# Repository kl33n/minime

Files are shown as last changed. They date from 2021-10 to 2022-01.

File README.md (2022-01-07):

# minime



3D printer mainboard Minime + Minime_mini, using a Raspberry Pi Pico (RP2040). Can be used on top of a Raspberry Pi or as standalone USB version.

The main goal of creating this little board was to design a 3D printer mainboard with Raspberry Pi Pico (RP2040) as MCU running Klipper firmware. Because of the limited number of I/O pins and ADC pins the board results in a very minimalistic (only 4 Stepper Driver on minime_mini) but also universal PCB.

Main Features:
- Running Klipper Firmware on Raspberry Pi Pico
- Raspberry Pi Host Version = use the minime and minime_mini as 3D Printer Mainboard with all primary features, like Heat_Bed and Hotend Control, Hotend Fan and Part Fan Control, X/Y/Z Endstop reading, Hotend Temperature and Bed Temperature reading, Probe reading, controlling 4 TMC2209 Stepper Driver
- The minime board can separately be used as standalone sensor board without the need of minime_mini as driver board and can directly be connected via usb to any Raspberry Pi Host
- Switchable between Endswitch and sensorless Homing via Solderjumper
- Switchable between +5V and +24V Probe via Solderjumper
- Switchable between +5V and +24V Fan Supply via Solderjumper
- Hotend Fan (Fan1, Sunon MF40100V1-1000C-G99) uses a 3 pin Header: VCC, GND and tachometer signal for savety reasons
- Fan tachometer signal can be set up in Klipper. If the speed of the Hotend Fan is not detectable, Klipper shuts down the printer (future option)
- Integrated bat85 diode (or similar) if using +24V probe
- Raspberry Pi Pico is used with pin headers to completely exchange the module if broken

Raspberry Pi Pico (with RP2040 Microcontroller):

- Raspberry Pi Host Version --> Raspberry Pi Pico has to be flashed with klipper.uf2 (UART Communication Option)
- Raspberry Pi Pico standalone Version --> Raspberry Pi Pico has to be flashed with klipper.uf2 (USB Communication Option)

136657995-72b43971-b637-41dd-9ba2-68b54d284a6b

A special thanks goes to Matt Shepcar (https://easyeda.com/matt_1626/) for his inspiring projects "Piglet print head control board" and "Raspberry Pi G-Code HAT"!

Future Modification:
- Switch from Raspberry Pi Pico Module to RP2040 integrated circuit
- Design two RP2040 MCU board, a host version with more than 4 stepper driver as driverboard and a separat sensorboard version including endswitches/hotend/bed/fans/temperatursensors and much more

Has to be continued!

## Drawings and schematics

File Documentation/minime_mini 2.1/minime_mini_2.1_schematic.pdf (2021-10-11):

# 4 J2

# D_EN C_DIAG B_DIAG A_DIAG A_STEP

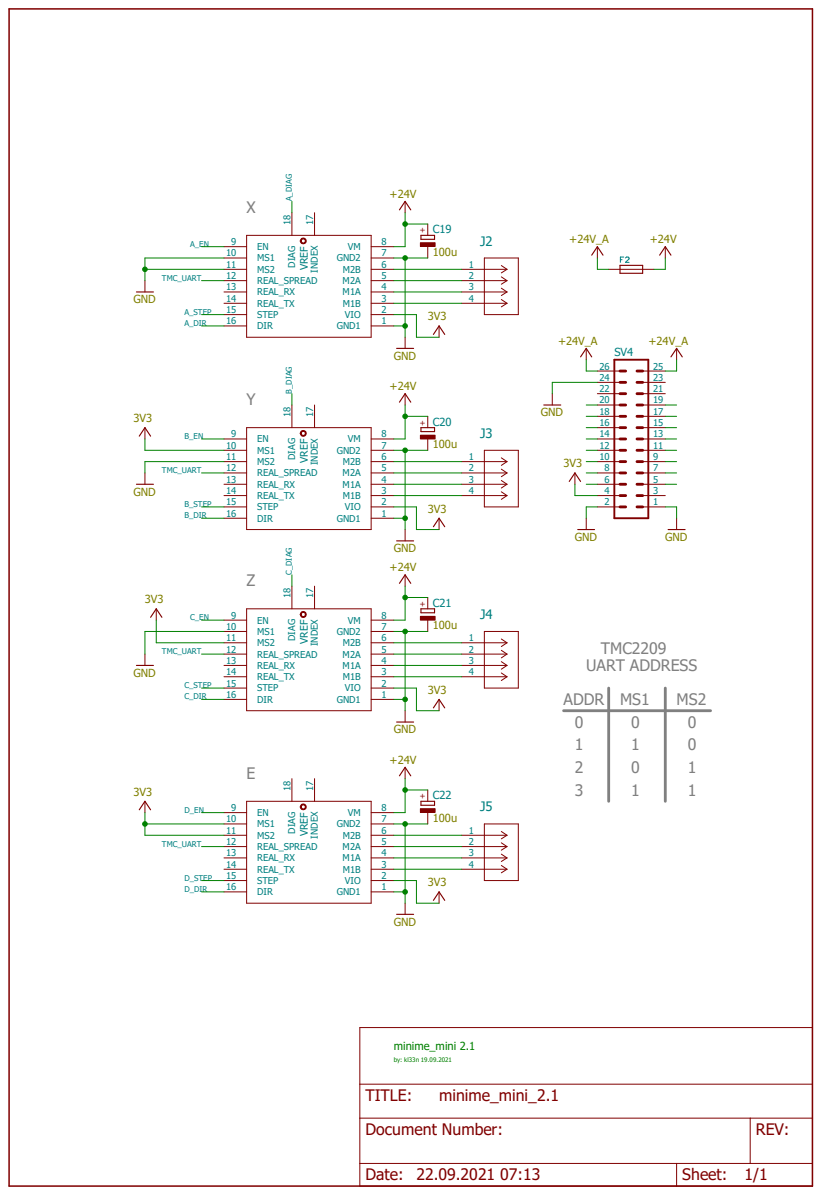
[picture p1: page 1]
GND; GND1; VIO; GND2; MS1 10 MS2 11 REAL_SPREAD 12 REAL_RX 13 REAL_TX 14 STEP 15; DIR 16; DIAG ¹⁸ VREF INDEX 17; C_DIR; C_STEP; D_DIR; D_STEP; A_DIR; B_STEP B_DIR; TMC_UART; TITLE:; minime_mini_2.1; by: kl33n 19.09.2021 minime_mini 2.1; ADDR; TMC2209 UART ADDRESS

Document Number: | REV:

Date: 22.09.2021 07:13 | Sheet: 1/1

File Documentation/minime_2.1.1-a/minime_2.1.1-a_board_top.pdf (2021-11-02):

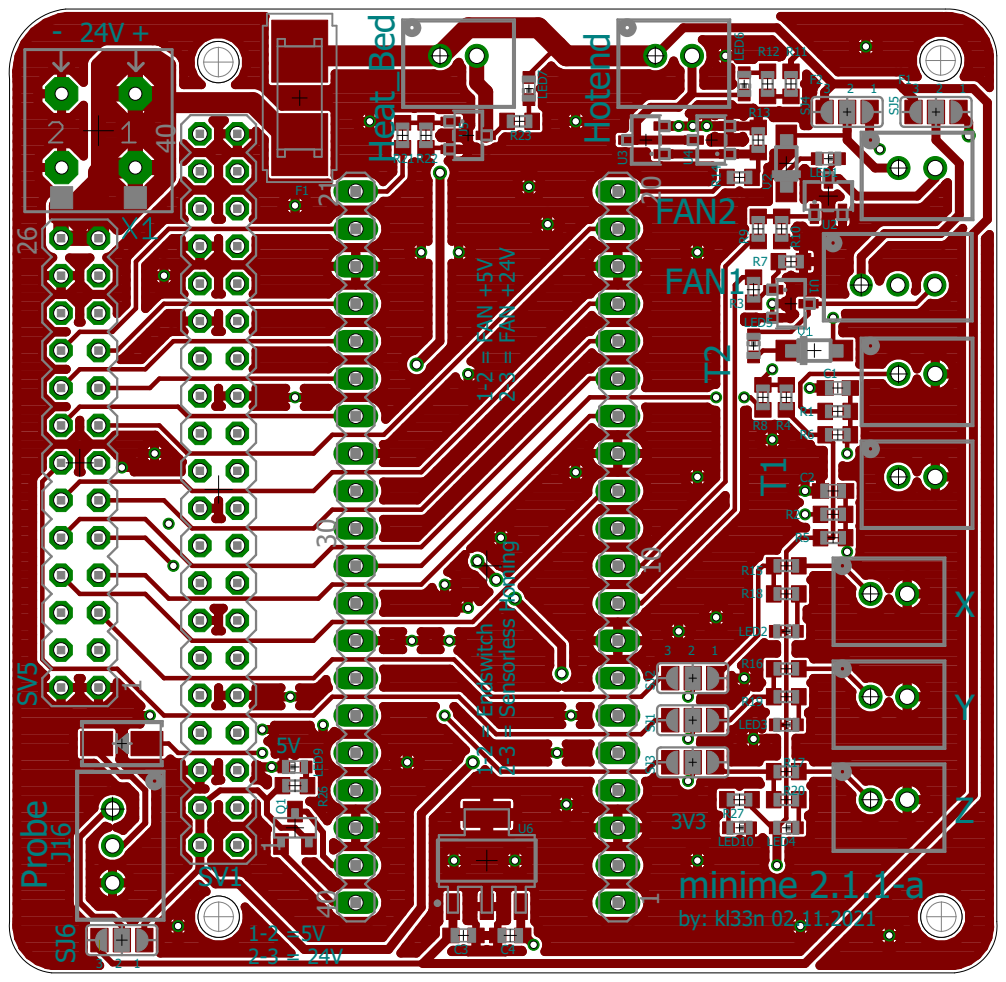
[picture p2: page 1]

1 20 10 21 40 30 1 40 1 26 - 24V + XYZ FAN1T2 T1 FAN2 Heat_Bed Hotend Probe3V3 5V 1-2 = Endswitch 2-3 = Sensorless Homing 3 2 1 minime 2.1.1-a by: kl33n 02.11.2021 1-2 = FAN +5V 2-3 = FAN +24V 3 2 1 3 2 1 1-2 =5V 3 2 1 2-3 = 24V F2 F1 R15 R16 R17 LED2 LED3LED4 R18 R19 R20 SV1 R1 R2 R3 R5R6 R7 U1 LED5 C1 C2 LED6 R12 R11 U3U4 R13 R14R21R22 U5 R23 LED7 LED9 R26 R27 LED10 SJ1 SJ2 SJ3 Q1 J16U6 C3 C4 F1 SV5 R8 R4 SJ5 SJ4 SJ6 LED1 R9 R10U2

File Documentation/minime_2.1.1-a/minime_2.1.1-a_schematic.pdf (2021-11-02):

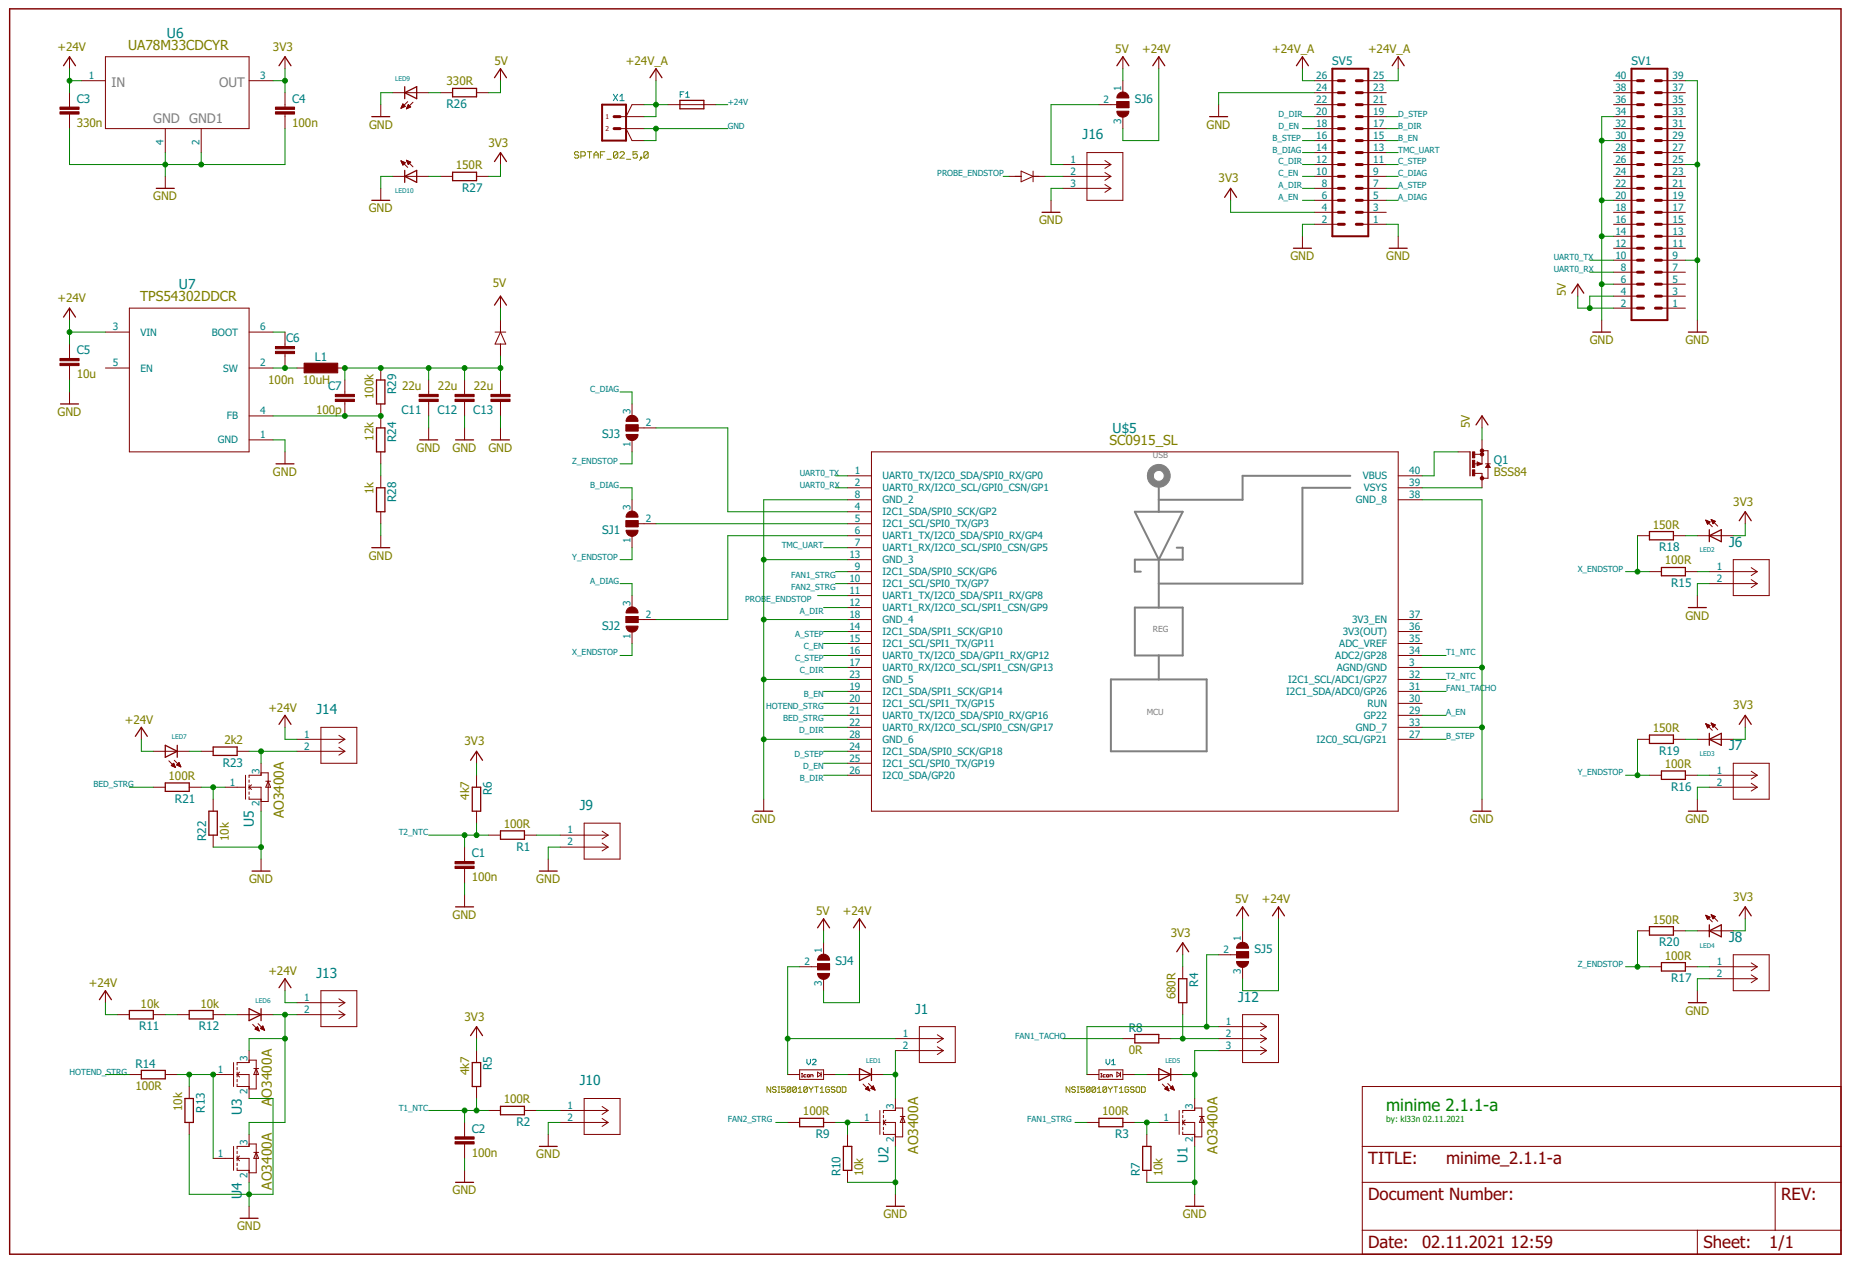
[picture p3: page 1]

REV: TITLE: Document Number: minime_2.1.1-a

Date: 02.11.2021 12:59 | Sheet: 1/1

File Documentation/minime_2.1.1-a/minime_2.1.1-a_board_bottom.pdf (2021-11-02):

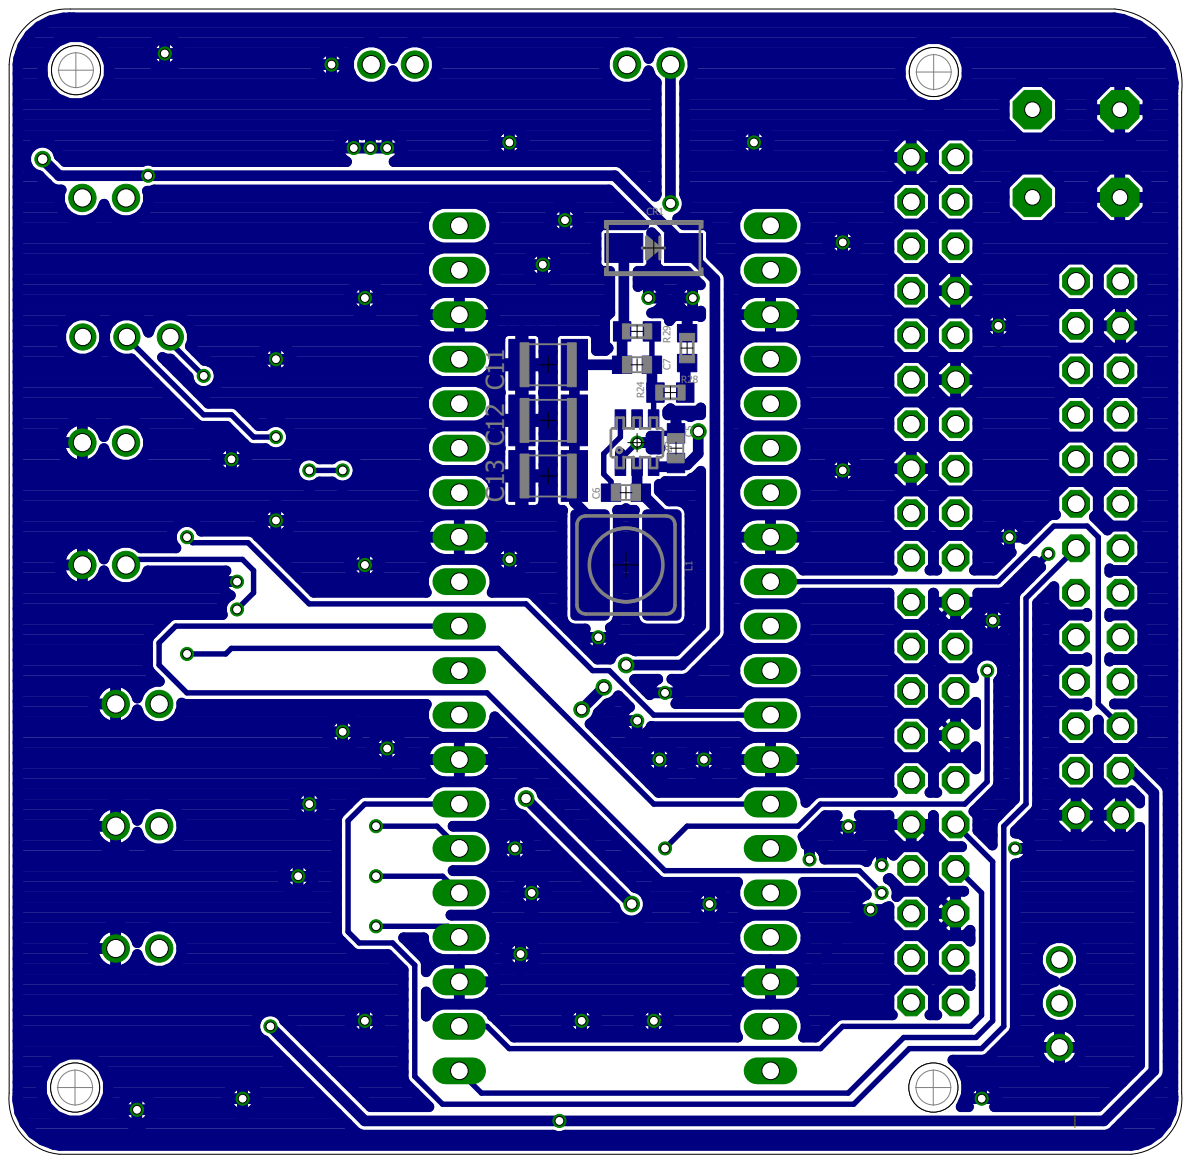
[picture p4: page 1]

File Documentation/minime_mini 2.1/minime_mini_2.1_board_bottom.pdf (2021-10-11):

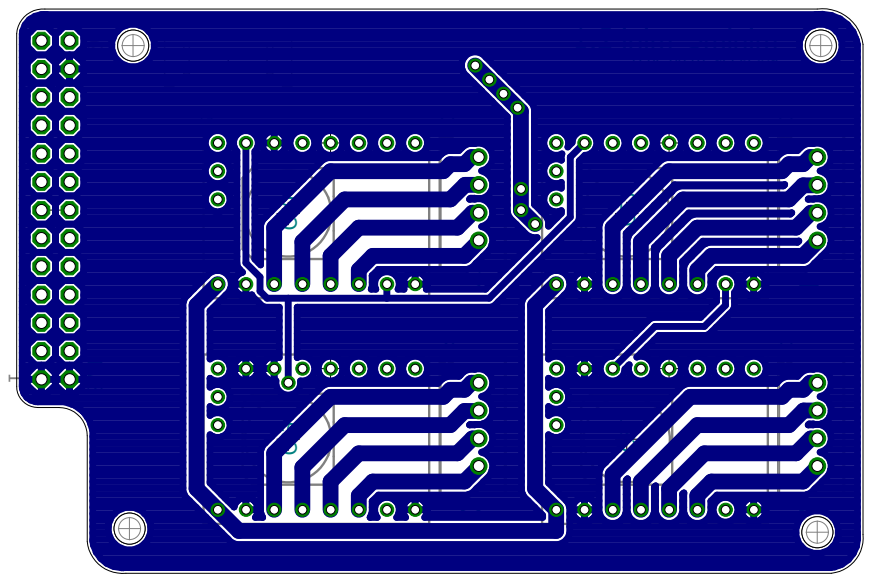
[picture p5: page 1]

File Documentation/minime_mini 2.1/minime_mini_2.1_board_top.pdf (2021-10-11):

# minime_mini 2.1

# by: kl33n 19.09.2021

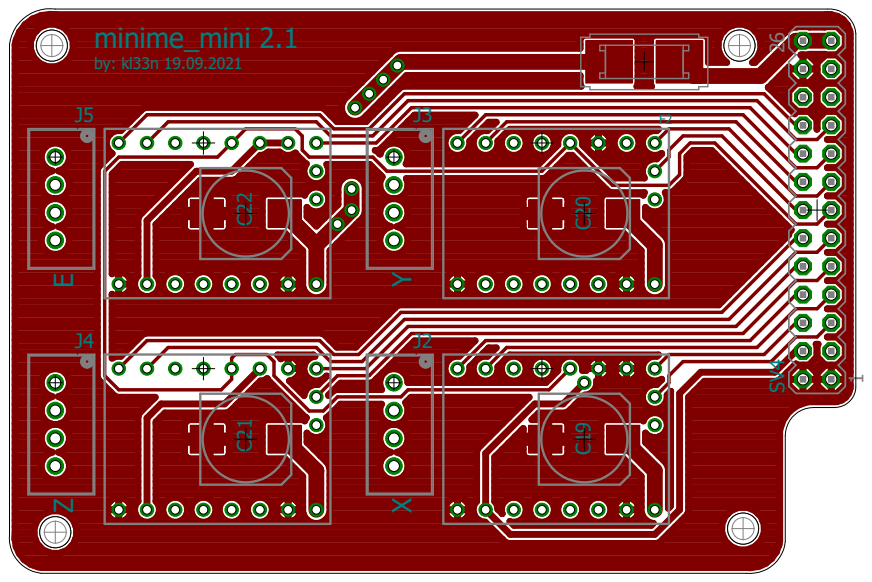
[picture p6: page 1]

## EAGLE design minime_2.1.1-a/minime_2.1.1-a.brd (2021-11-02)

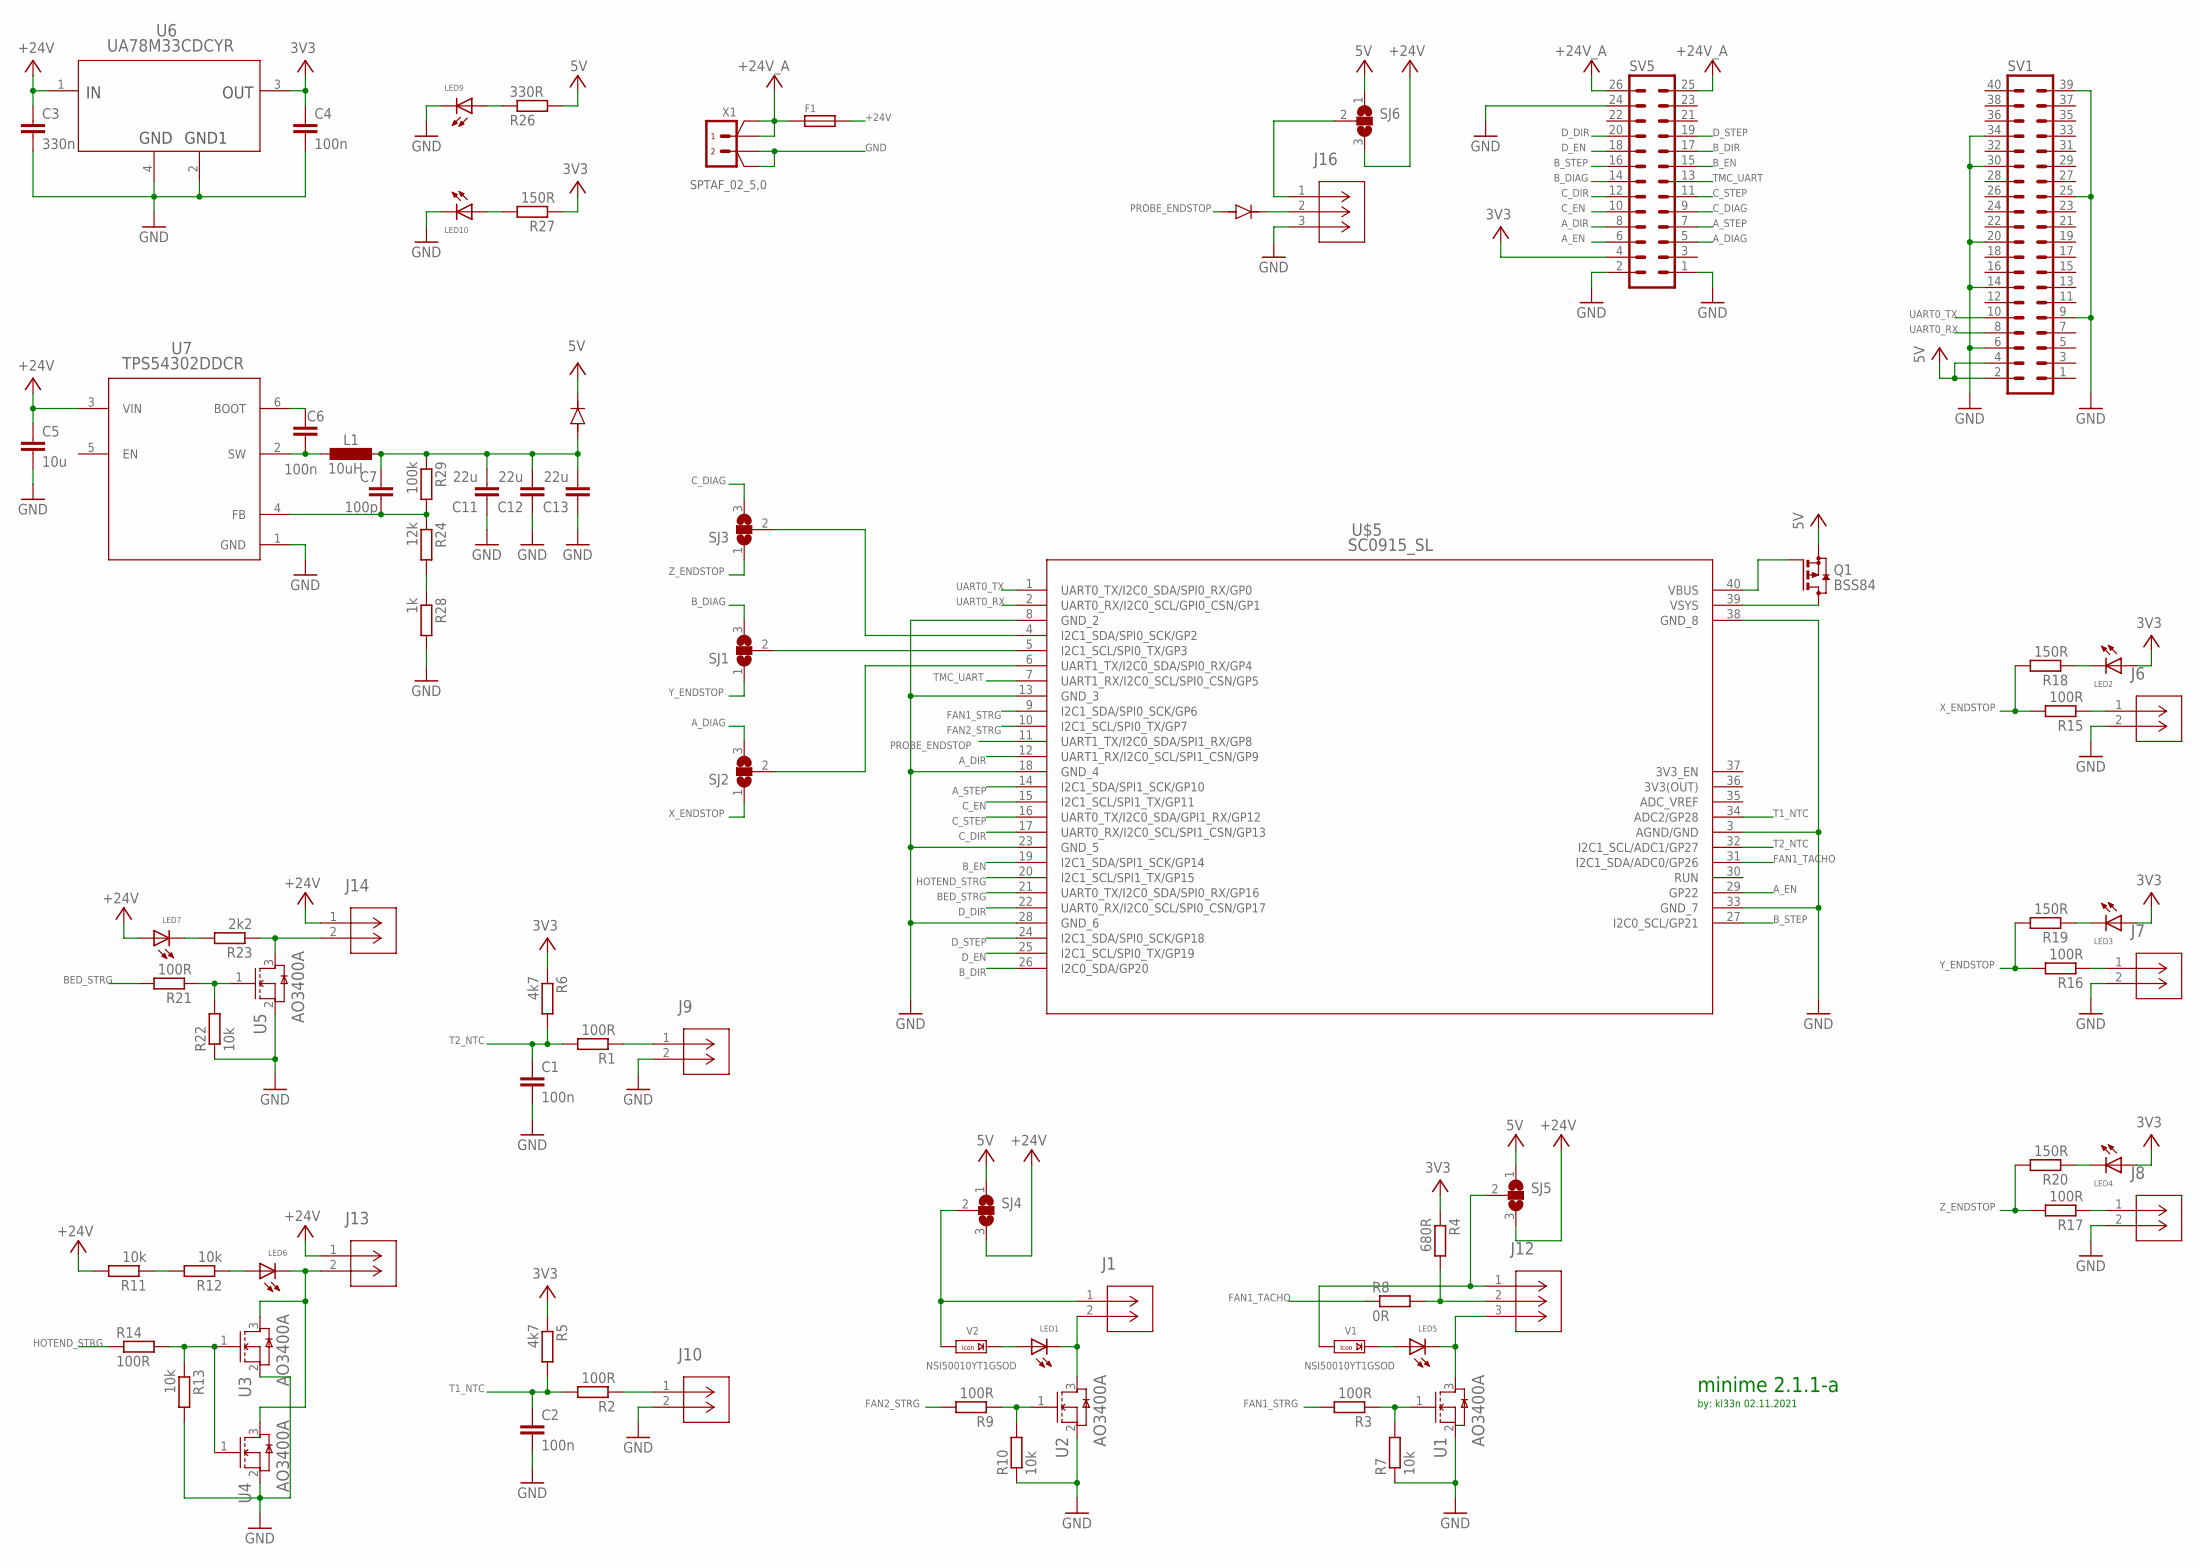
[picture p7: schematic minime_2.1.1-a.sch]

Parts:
C1, C2, C4, C6: 100n; C0603
C3: 330n; C0603
C5: 10u; C0603
C7: 100p; C0603
C11, C12, C13: 22u; C1210K
CR1: SS54; DIODE_DO214AC
CR2: SS14; DIODE_DO214AC
F1: FUSE/SERIE154; FUSE/NANO-OMNI
J1, J6, J7, J8, J9, J10, J13, J14: B2B-XH-A(LF)(SN); CONN_B2B-XH-A(LF)(SN)_JST
J12, J16: B3B-XH-A(LF)(SN); CONN_B3B-XH-A_JST
L1: 10uH; POWER-CHOKE_WE-TPC
LED1, LED2, LED3, LED4, LED5, LED6, LED7, LED9, LED10: LEDCHIP-LED0603; CHIP-LED0603
Q1: BSS84; SOT23
R1, R2, R3, R9, R14, R15, R16, R17, R21: 100R; R0603
R4: 680R; R0603
R5, R6: 4k7; R0603
R7, R10, R11, R12, R13, R22: 10k; R0603
R8: 0R; R0603
R18, R19, R20, R27: 150R; R0603
R23: 2k2; R0603
R24: 12k; R0603
R26: 330R; R0603
R28: 1k; R0603
R29: 100k; R0603
SJ1, SJ2, SJ3, SJ4, SJ5, SJ6: SJ2W; SJ_2
SV1: MA20-2
SV5: MA13-2
U1, U2, U3, U4, U5: AO3400A; SOT-23-3L_AOS
U6: UA78M33CDCYR; DCY0004A_N
U7: TPS54302DDCR; DDC0006A_N
U$5: SC0915_SL; STIFTLEISTE
V1, V2: NSI50010YT1GSOD; SOD123
X1: SPTAF_02_5,0; 5-2

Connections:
3V3: C4.1, LED2.A, LED3.A, LED4.A, R4.1, R5.1, R6.1, R27.1, SV5.4, U6.3 (OUTPUT)
3V3_EN: U$5.37 (3V3_EN)
5V: CR1.1, Q1.2 (S), R26.2, SJ4.1, SJ5.1, SJ6.1, SV1.2, SV1.4
+24V: C3.1, C5.1, F1.2, J13.1, J14.1, LED7.A, R11.2, SJ4.3, SJ5.3, SJ6.3, U6.1 (INPUT), U7.3 (VIN)
+24V_A: F1.1, SV5.25, SV5.26, X1.1, X1.1A
ADC_VREF: U$5.35 (ADC_VREF)
A_DIAG: SJ2.3, SV5.5
A_DIAG_X_ENDSTOP: SJ2.2, U$5.6 (UART1_TX/I2C0_SDA/SPI0_RX/GP4)
A_DIR: SV5.8, U$5.12 (UART1_RX/I2C0_SCL/SPI1_CSN/GP9)
A_EN: SV5.6, U$5.29 (GP22)
A_STEP: SV5.7, U$5.14 (I2C1_SDA/SPI1_SCK/GP10)
BED_STRG: R21.2, U$5.21 (UART0_TX/I2C0_SDA/SPI0_RX/GP16)
B_DIAG: SJ1.3, SV5.14
B_DIAG_Y_ENDSTOP: SJ1.2, U$5.5 (I2C1_SCL/SPI0_TX/GP3)
B_DIR: SV5.17, U$5.26 (I2C0_SDA/GP20)
B_EN: SV5.15, U$5.19 (I2C1_SDA/SPI1_SCK/GP14)
B_STEP: SV5.16, U$5.27 (I2C0_SCL/GP21)
C_DIAG: SJ3.3, SV5.9
C_DIAG_Z_ENDSTOP: SJ3.2, U$5.4 (I2C1_SDA/SPI0_SCK/GP2)
C_DIR: SV5.12, U$5.17 (UART0_RX/I2C0_SCL/SPI1_CSN/GP13)
C_EN: SV5.10, U$5.15 (I2C1_SCL/SPI1_TX/GP11)
C_STEP: SV5.11, U$5.16 (UART0_TX/I2C0_SDA/GPI1_RX/GP12)
D_DIR: SV5.20, U$5.22 (UART0_RX/I2C0_SCL/SPI0_CSN/GP17)
D_EN: SV5.18, U$5.25 (I2C1_SCL/SPI0_TX/GP19)
D_STEP: SV5.19, U$5.24 (I2C1_SDA/SPI0_SCK/GP18)
FAN1_STRG: R3.2, U$5.9 (I2C1_SDA/SPI0_SCK/GP6)
FAN1_TACHO: R8.1, U$5.31 (I2C1_SDA/ADC0/GP26)
FAN2_STRG: R9.2, U$5.10 (I2C1_SCL/SPI0_TX/GP7)
GND: C1.2, C2.2, C3.2, C4.2, C5.2, C11.1, C12.1, C13.1, J6.2, J7.2, J8.2, J9.2, J10.2, J16.3, LED9.C, LED10.C, R7.1, R10.1, R13.2, R22.1, R28.2, SV1.6, SV1.9, SV1.14, SV1.20, SV1.25, SV1.30, SV1.34, SV1.39, SV5.1, SV5.2, SV5.24, U1.2 (S), U2.2 (S), U3.2 (S), U4.2 (S), U5.2 (S), U6.2 (COMMON_2), U6.4 (COMMON), U7.1 (GND), U$5.3 (AGND/GND), U$5.8 (GND_2), U$5.13 (GND_3), U$5.18 (GND_4), U$5.23 (GND_5), U$5.28 (GND_6), U$5.33 (GND_7), U$5.38 (GND_8), X1.2, X1.2A
HOTEND_STRG: R14.1, U$5.20 (I2C1_SCL/SPI1_TX/GP15)
unnamed: LED6.A, R12.1
unnamed: R11.1, R12.2
unnamed: R21.1, R22.2, U5.1 (G)
unnamed: R13.1, R14.2, U3.1 (G), U4.1 (G)
unnamed: J16.1, SJ6.2
unnamed: LED5.A, V1.C (K)
unnamed: R9.1, R10.2, U2.1 (G)
unnamed: LED1.A, V2.C (K)
unnamed: J14.2, R23.1, U5.3 (D)
unnamed: J1.2, LED1.C, U2.3 (D)
unnamed: J8.1, R17.1
unnamed: J7.1, R16.1
unnamed: J6.1, R15.1
unnamed: J10.1, R2.1
unnamed: LED2.C, R18.1
unnamed: LED3.C, R19.1
unnamed: J9.1, R1.1
unnamed: J12.2, R4.2, R8.2
unnamed: LED4.C, R20.1
unnamed: R3.1, R7.2, U1.1 (G)
unnamed: LED7.C, R23.2
unnamed: J12.3, LED5.C, U1.3 (D)
unnamed: J13.2, LED6.C, U3.3 (D), U4.3 (D)
unnamed: LED9.A, R26.1
unnamed: J12.1, SJ5.2, V1.A
unnamed: LED10.A, R27.2
unnamed: J1.1, SJ4.2, V2.A
unnamed: CR2.1, J16.2
unnamed: R24.2, R28.1
unnamed: C6.1, U7.6 (BOOT)
unnamed: C6.2, L1.2, U7.2 (SW)
unnamed: C7.2, R24.1, R29.2, U7.4 (FB)
unnamed: C7.1, C11.2, C12.2, C13.2, CR1.2, L1.1, R29.1
PROBE_ENDSTOP: CR2.2, U$5.11 (UART1_TX/I2C0_SDA/SPI1_RX/GP8)
T1_NTC: C2.1, R2.2, R5.2, U$5.34 (ADC2/GP28)
T2_NTC: C1.1, R1.2, R6.2, U$5.32 (I2C1_SCL/ADC1/GP27)
TMC_UART: SV5.13, U$5.7 (UART1_RX/I2C0_SCL/SPI0_CSN/GP5)
UART0_RX: SV1.8, U$5.2 (UART0_RX/I2C0_SCL/GPI0_CSN/GP1)
UART0_TX: SV1.10, U$5.1 (UART0_TX/I2C0_SDA/SPI0_RX/GP0)
VBUS: Q1.1 (G), U$5.40 (VBUS)
VSYS: Q1.3 (D), U$5.39 (VSYS)
X_ENDSTOP: R15.2, R18.2, SJ2.1
Y_ENDSTOP: R16.2, R19.2, SJ1.1
Z_ENDSTOP: R17.2, R20.2, SJ3.1

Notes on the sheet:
by: kl33n 02.11.2021
minime 2.1.1-a

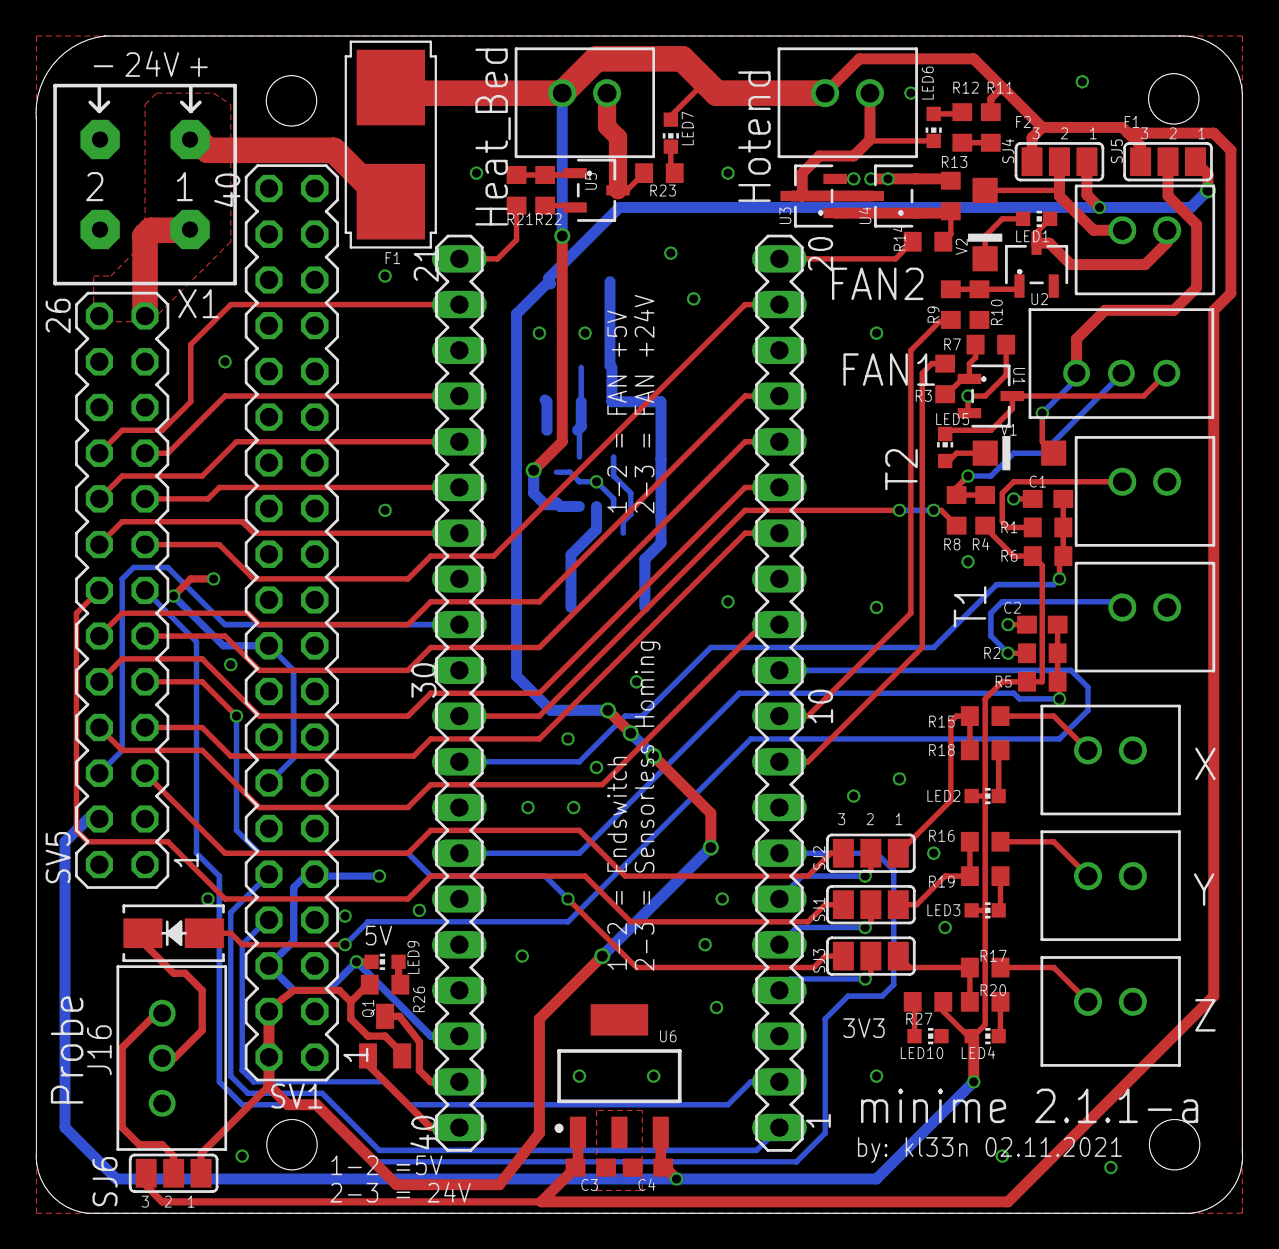
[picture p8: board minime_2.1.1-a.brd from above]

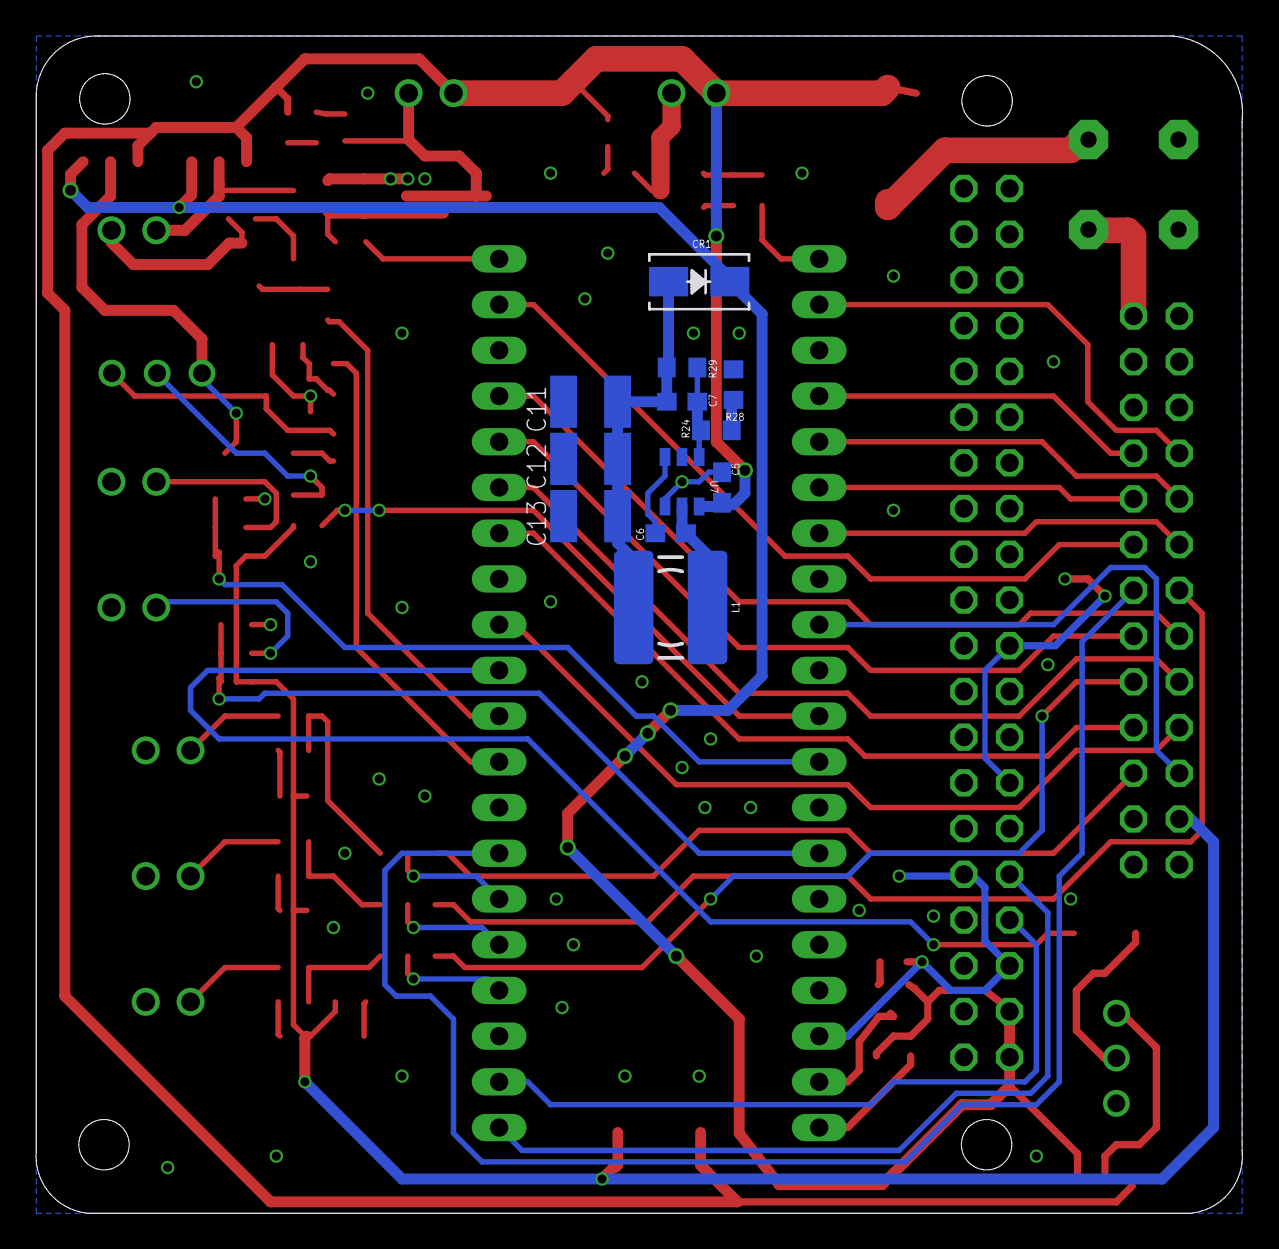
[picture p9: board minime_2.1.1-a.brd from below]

Board: 2 copper layers, 67.0 x 65.4 mm, 81 parts (12 on the bottom side), 72 nets.

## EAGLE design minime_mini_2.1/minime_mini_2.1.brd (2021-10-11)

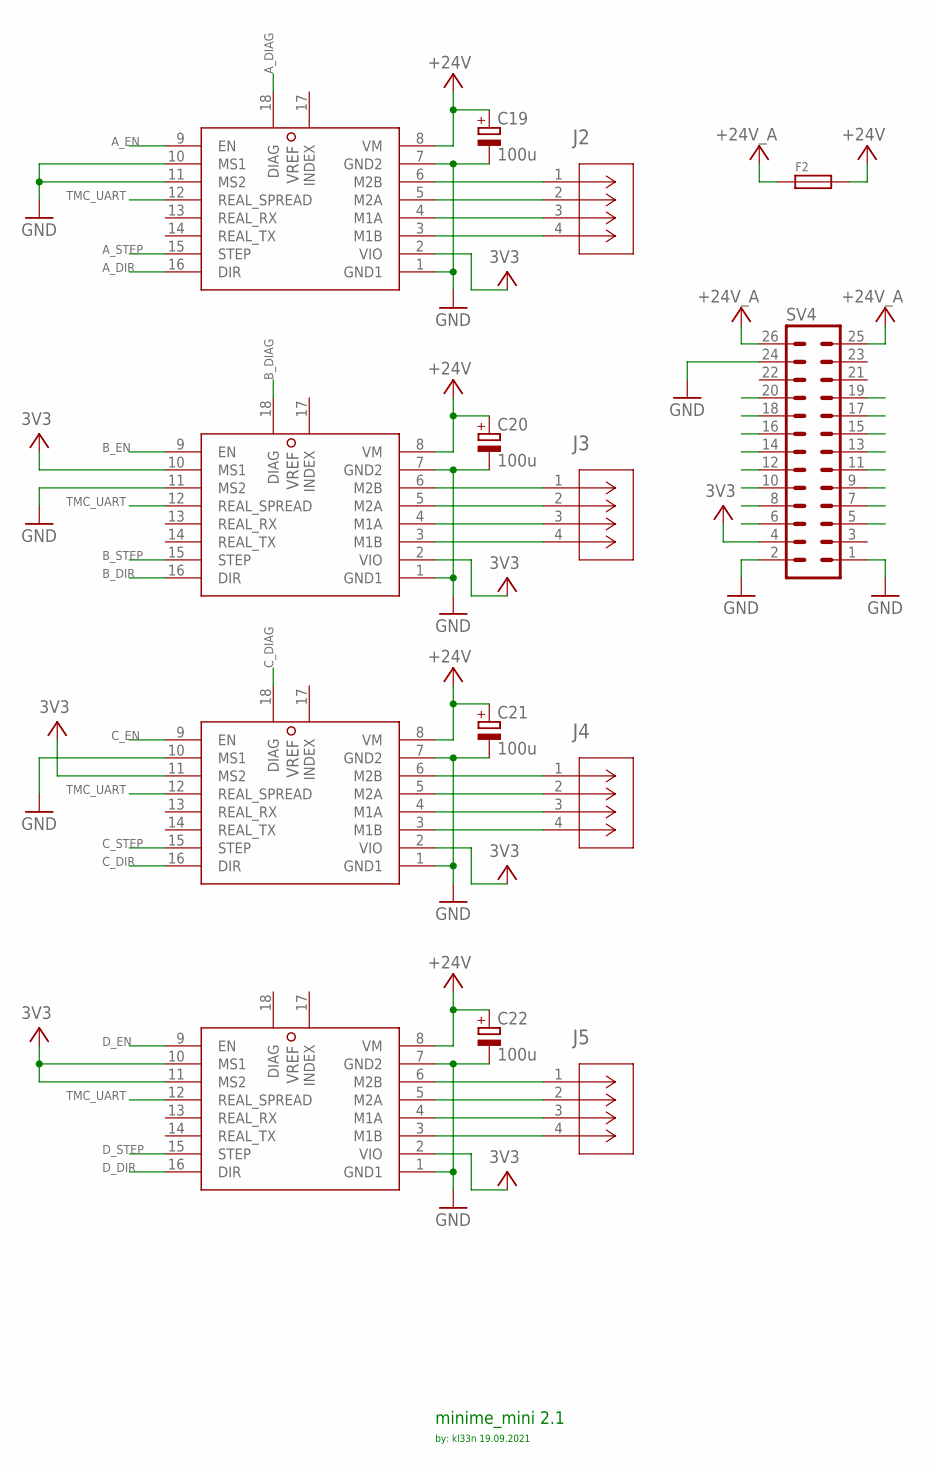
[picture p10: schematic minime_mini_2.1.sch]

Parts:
C19, C20, C21, C22: 100u; 175TMP-0810
F2: FUSE/SERIE154; FUSE/NANO-OMNI
J2, J3, J4, J5: B4B-XH-AM(LF)(SN); CONN_B4B-XH-AM_JST
SV4: MA13-2
U$1, U$2, U$3, U$4: TMC2209

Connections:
3V3: SV4.4, U$1.2 (VIO), U$1.10 (MS1), U$2.2 (VIO), U$3.2 (VIO), U$3.11 (MS2), U$4.2 (VIO), U$4.10 (MS1), U$4.11 (MS2)
+24V: C19.+, C20.+, C21.+, C22.+, F2.2, U$1.8 (VM), U$2.8 (VM), U$3.8 (VM), U$4.8 (VM)
+24V_A: F2.1, SV4.25, SV4.26
A_DIAG: SV4.5, U$2.18 (DIAG)
A_DIR: SV4.8, U$2.16 (DIR)
A_EN: SV4.6, U$2.9 (EN)
A_STEP: SV4.7, U$2.15 (STEP)
B_DIAG: SV4.14, U$1.18 (DIAG)
B_DIR: SV4.17, U$1.16 (DIR)
B_EN: SV4.15, U$1.9 (EN)
B_STEP: SV4.16, U$1.15 (STEP)
C_DIAG: SV4.9, U$3.18 (DIAG)
C_DIR: SV4.12, U$3.16 (DIR)
C_EN: SV4.10, U$3.9 (EN)
C_STEP: SV4.11, U$3.15 (STEP)
D_DIR: SV4.20, U$4.16 (DIR)
D_EN: SV4.18, U$4.9 (EN)
D_STEP: SV4.19, U$4.15 (STEP)
GND: C19.-, C20.-, C21.-, C22.-, SV4.1, SV4.2, SV4.24, U$1.1 (GND1), U$1.7 (GND2), U$1.11 (MS2), U$2.1 (GND1), U$2.7 (GND2), U$2.10 (MS1), U$2.11 (MS2), U$3.1 (GND1), U$3.7 (GND2), U$3.10 (MS1), U$4.1 (GND1), U$4.7 (GND2)
unnamed: J2.1, U$2.6 (M2B)
unnamed: J2.2, U$2.5 (M2A)
unnamed: J2.3, U$2.4 (M1A)
unnamed: J2.4, U$2.3 (M1B)
unnamed: J3.1, U$1.6 (M2B)
unnamed: J3.2, U$1.5 (M2A)
unnamed: J3.3, U$1.4 (M1A)
unnamed: J3.4, U$1.3 (M1B)
unnamed: J4.1, U$3.6 (M2B)
unnamed: J4.2, U$3.5 (M2A)
unnamed: J4.3, U$3.4 (M1A)
unnamed: J4.4, U$3.3 (M1B)
unnamed: J5.1, U$4.6 (M2B)
unnamed: J5.2, U$4.5 (M2A)
unnamed: J5.3, U$4.4 (M1A)
unnamed: J5.4, U$4.3 (M1B)
TMC_UART: SV4.13, U$1.12 (REAL_SPREAD), U$2.12 (REAL_SPREAD), U$3.12 (REAL_SPREAD), U$4.12 (REAL_SPREAD)

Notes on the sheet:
by: kl33n 19.09.2021
minime_mini 2.1

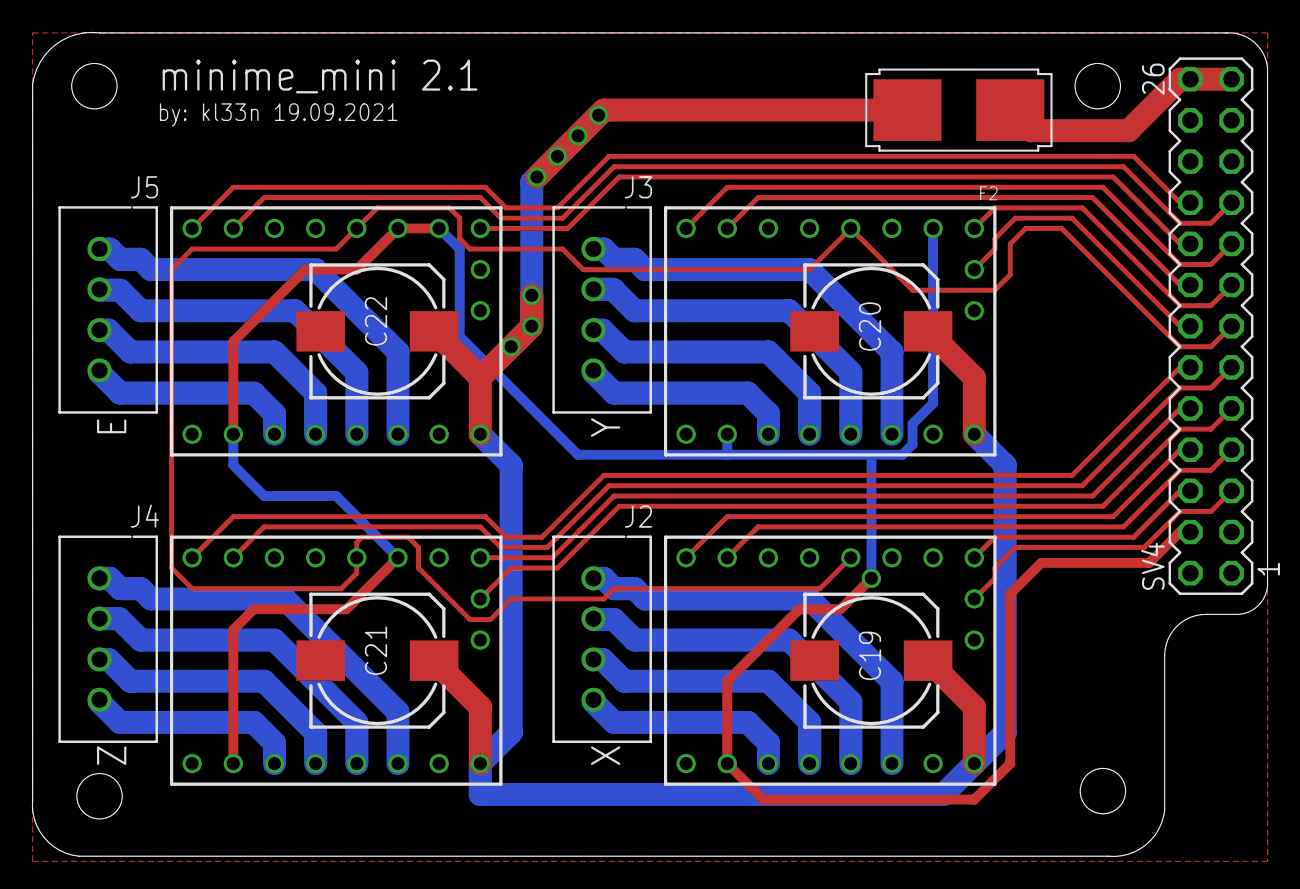
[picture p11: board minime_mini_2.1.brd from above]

Board: 2 copper layers, 76.2 x 50.8 mm, 14 parts (0 on the bottom side), 36 nets.

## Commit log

2021-10-11 new dir structure
    [minime_2.1.1.brd, minime_2.1.1.sch, minime_2.1.brd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]
2021-10-21 removed Archive
    [minime_2.1.brd, minime_2.1.sch]
2021-11-02 new version 2.1.1-a
    [minime_2.1.1-a.brd, minime_2.1.1-a.sch]

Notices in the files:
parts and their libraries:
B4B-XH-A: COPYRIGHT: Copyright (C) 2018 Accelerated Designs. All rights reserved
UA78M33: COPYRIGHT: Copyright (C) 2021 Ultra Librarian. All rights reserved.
